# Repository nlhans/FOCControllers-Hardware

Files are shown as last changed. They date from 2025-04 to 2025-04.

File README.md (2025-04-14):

# FOCControllers
Exploring the world of FOC with BLDC/Steppers for custom haptic/force feedback in game controllers

Design is WIP.

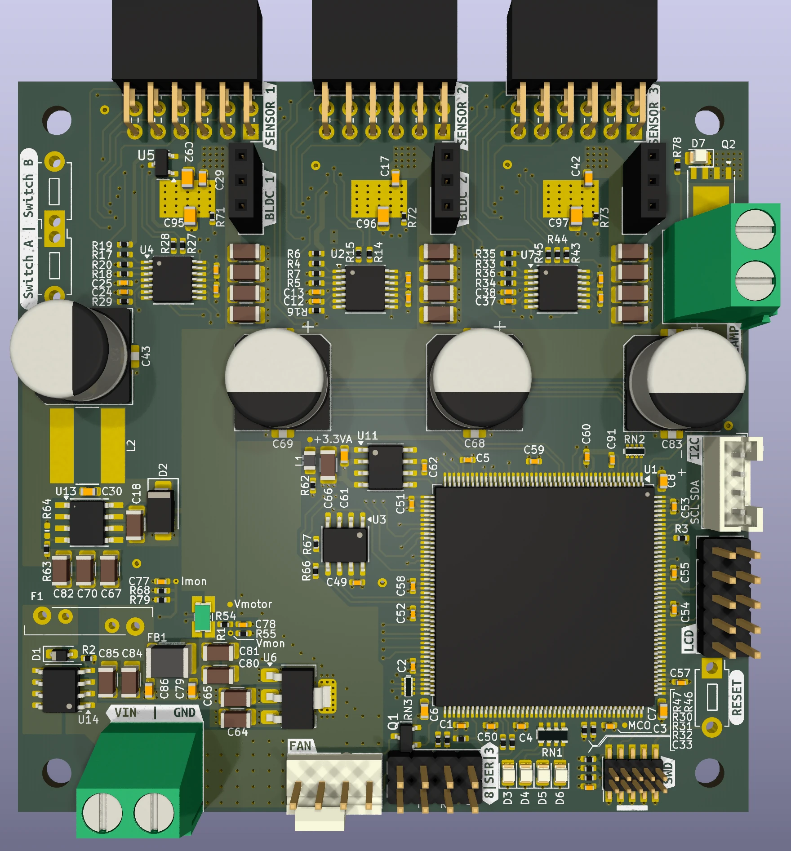
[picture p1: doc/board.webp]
PCB


## MCU
After some exploration, I've chosen to base this design around the STM32H725. There were several close runner ups, including some STM32G4 and F7 parts, and most honourable mention the RP2350. However, the RP2350 was not available from Mouser etc. at the time I started CAD. 
The secondary reason for the STM32H725 is that I still have a handful of these chips unassigned to a project in my parts bin. Considering they weren't cheap while coming in the "large brick" LQFP-176 package, this seemed like a good excuse to finally use them (-: 

Joking aside, this part is quite well suited for experiments with BLDC. Empirical observations using a Nucleo-H743 and the Arduino SimpleFOC library showed that the loopFOC() and move() functions take approximately 3.8 - 4.0us to execute on this chip (approx 1900 CPU cycles). This does not include sensor I/O. That means that running the FOC loop at 5-25kHz (depending on the position sensor datarate) will use around 2-10\% of CPU time. However, in this design I will be using this chip to drive 3 motors, which could bring up the CPU load to 30\%. 

This CPU time excludes I/O time from I2C/SPI bus transfers, or ADC data retrieval, "actual" FOC with DC current feedback, and more importantly, and force feedback algorithms. I would expect when this is all included that 25kHz loop speed would be quite the challenge.

I have also considered the RP2040, as I've used it for some exploration before concluding this design. However its lack of FPU and Cortex-M0+ could not do FOC loop calculations at more than 1kHz due to widespread floating point usage in SimpleFOC. Perhaps 2kHz was attainable when the slow I2C I/O is offloaded to the second core.. but 2kHz is still not a terrific loop speed. It didn't make sense to go through all that effort.

## Motor Driver
I have chosen to use the DRV8316C BLDC driver from Texas Instruments. This chip can use 6-PWM or 3-PWM mode with ENABLE input. The latter is necessary for SimpleFOC implementation of PWM and truth table to the (half-)H bridge drivers. Previous experiments with cheap DRV8833 boards were able to drive a BLDC motor, however, it was not controlling the DRV8833s properly due to its truth table orientated at brushed motor control (long story..). 

Moreover, the DRV8316C chip can operate with 24V supply. and drive 3-5A into motors. I plan to use this magnitude of power for developing an active pedal for simrig racing. These typically require motors in the order of 60-90Watt peak. 

The whole board will be fused for a continuous current of 5A. This may seem awkward to divide across 3 channels, but I expect the duty cycle and concurrent power output to be quite low for this application.

##  Sensing
The board contains, per motor channel, the interfaces for the following sensors:

- I2C magnetic encoders (e.g. As5600)
- SPI or Infineon SSC magnetic encoders (e.g. TLE5012B or TLI5012B)
- Lineair Potentiometer
- NTC for motor temperature
- Current Sense for all 3 coil outputs

The analog sensor channels are connected to a dedicated ADC on the STM32H7 each. The chip will be programmed to convert all channels on each FOC cycle.

All analog channels are referenced against a 3.0V voltage reference. BLDC channel 1 contains a 3.0V regulator to power the analog electronics for all 3 motor channels.

## Other stuff
The PCB contains several support functions which should aid for a configurable & robust driver:

- I2C 24AAxx EEPROM (bitbanged)
- I2C temperature sensor near driver of channel 2 (bitbanged)
- Voltage/Current monitor of input supply
- 5V/Vin 4-pin PWM fan with tacho readout. The board has a 80x80mm form factor in case it runs hot.
- Power clamp to dump regen power (if necessary).
- SPI interface for driving a small LCD
- I2C Grove Connector (hardware I2C)
- 2 UARTs
- 4 Debug LEDs
- 2 Push Buttons
- SWD debug

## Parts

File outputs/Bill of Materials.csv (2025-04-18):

Id | Designator | Footprint | Quantity | Designation | Supplier and ref
1 | R82,R81,R67,R78,R55,R66,R56,R59,R60,R76,R61,R58,R77,R57 | Nice_0402R | 14 | 1k
2 | D9,D8,D6,D5,D7,D3,D4 | LED_0805_2012Metric | 7 | APT2012SYCK
3 | C97,C96,C95,C92,C8,C6,C7 | Nice_0603C | 7 | 2.2u
4 | R68,R79 | Nice_0402R | 2 | 15k
5 | R19,R5,R34,R32,R35,R8,R36,R4,R6,R7,R20,R54,R33,R31,R3,R17,R18,R30,R9 | Nice_0402R | 19 | 10k
6 | TP54,TP56,TP53,TP59,TP55,TP22,TP75,TP47,TP36,TP49,TP70,TP69,TP41,TP74,TP35,TP23,TP12,TP20,TP24,TP66,TP31,TP40,TP32,TP48,TP76,TP39,TP17,TP43,TP65,TP16,TP34,TP64,TP63,TP71,TP25,TP61,TP58,TP51,TP15,TP73,TP52,TP33,TP10,TP68,TP42,TP14,TP28,TP29,TP77,TP38,TP26,TP45,TP44,TP11,TP72,TP13,TP46,TP62,TP30,TP21,TP57,TP37,TP67,TP19,TP60,TP27,TP50,TP18 | TP_0.6mm | 68 | TestPoint
7 | C50,C91,C25,C51,C3,C49,C57,C77,C78,C33,C2,C55,C54,C60,C5,C4,C13,C53,C58,C59,C52,C1,C38,C56,C40,C9,C89,C34,C15,C88,C27,C21,C63,C26 | Nice_0402C | 34 | 100n
8 | R44,R29,R15,R27,R45,R43,R14,R28,R16 | Nice_0402R | 9 | 820R
9 | J12,J5 | TerminalBlock_Phoenix_MKDS-1,5-2_1x02_P5.00mm_Horizontal | 2 | Screw_Terminal_01x02
10 | C72,C31,C20,C74,C85,C19,C18,C84,C66,C80,C70,C75,C65,C71,C82,C76,C67,C81,C44,C73,C45,C64,C32 | C_1206_3216Metric | 23 | 10u
11 | R2 | Nice_0402R | 1 | 100k
12 | SW3,SW2,SW1 | SW_PUSH_1P1T_6x3.5mm_H5.0_APEM_MJTP1250 | 3 | SW_Push
13 | R71,R47,R46,R73,R63,R72,R49 | Nice_0402R | 7 | 0R
14 | U2,U4,U7 | TSSOP-14_4.4x5mm_P0.65mm | 3 | LM324
15 | J11,J9 | PinHeader_1x04_P2.54mm_Vertical | 2 | Conn_01x04
16 | R69,R75,R62,R74,R70 | Nice_0402R | 5 | 100R
17 | J4 | PinHeader_2x05_P2.54mm_Vertical | 1 | Conn_02x05_Odd_Even
18 | R1 | R_Shunt_Ohmite_LVK12 | 1 | LVK12R020
19 | U3 | SOIC-8_3.9x4.9mm_P1.27mm | 1 | 24LC64
20 | SWD1 | PinHeader_2x05_P1.27mm_Vertical_SMD | 1 | Conn_02x05_Odd_Even
21 | C11,C12,C35,C23,C36,C37,C22,C10,C24 | Nice_0402C | 9 | 100p
22 | R80 | Nice_0402DNP | 1 | DNP
23 | U6 | SOT-223-3_TabPin2 | 1 | AMS1117-3.3
24 | C86,C79,C90,C42,C17,C29 | Nice_0603C | 6 | 100n
25 | J8,J7,J6 | PinSocket_1x03_P2.54mm_Vertical | 3 | Conn_01x03_Pin
26 | M1 | FanPinHeader_1x04_P2.54mm_Vertical | 1 | Fan_Tacho_PWM
27 | FB1 | L_1812_4532Metric | 1 | 74279223560
28 | J1,J3,J2 | PinSocket_2x06_P2.54mm_Horizontal | 3 | Conn_02x06_Odd_Even
29 | RN1 | R_Array_Convex_4x0603 | 1 | EXB-38V102JV
30 | RN2,RN3,RN4,RN5 | R_Array_Concave_4x0402 | 4 | EXB-N8N220JX
31 | Q1 | SOT-23 | 1 | 2N7002
32 | L2 | L_Bourns-SRN8040_8x8.15mm | 1 | 22u
33 | C69,C68,C83 | CP_Elec_10x10.5 | 3 | 330uF
34 | C61,C28,C16,C41 | Nice_0603C | 4 | 1u
35 | C30 | Nice_0603C | 1 | 10n
36 | U11 | SOIC-8_3.9x4.9mm_P1.27mm | 1 | MCP1501-25E/SN
37 | U1 | LQFP-176_24x24mm_P0.5mm | 1 | STM32H725IGTx
38 | F1 | LIttelfuse_30R | 1 | 30R500U
39 | R64,R48 | Nice_0402DNP | 2 | TBD
40 | D2 | D_SMA | 1 | SS16
41 | L1 | L_0805_2012Metric | 1 | BLM18AG471SN1D
42 | C43 | CP_Elec_8x10.5 | 1 | 330uF
43 | U14 | SOIC-8_3.9x4.9mm_P1.27mm | 1 | Si4435DDY
44 | U13 | TI_SO-PowerPAD-8 | 1 | LM22676MR-5
45 | J10 | JST_PH_B4B-PH-K_1x04_P2.00mm_Vertical | 1 | Conn_01x04
46 | D1 | D_SOD-323_HandSoldering | 1 | BZX384-B10,115
47 | Q2 | PowerPAK_SO-8_Single | 1 | SIR422DP-T1-GE3
48 | U5 | SOT-23 | 1 | AP7375-30SA-7
49 | C62 | Nice_0402C | 1 | 1n
50 | Y1 | Crystal_SMD_3225-4Pin_3.2x2.5mm | 1 | ECS-250-18-33-JGN-TR3
51 | U16,U10,U15 | VQFN40_RGF_TEX | 3 | DRV8316CR
52 | U12 | WSON-8-1EP_2x2mm_P0.5mm_EP0.9x1.6mm_ThermalVias | 1 | TMP1075DSG
53 | C39,C48,C87 | Nice_0603C | 3 | 47n
54 | U17 | SOT-23 | 1 | ZXCT1109
55 | R65,R51,R50,R52 | Nice_0402R | 4 | 470R
56 | TP6,TP1,TP4,TP7,TP2,TP5,TP8,TP3 | TestPoint_THTPad_D1.0mm_Drill0.5mm | 8 | TestPoint
57 | C46,C47 | Nice_0402C | 2 | 18p

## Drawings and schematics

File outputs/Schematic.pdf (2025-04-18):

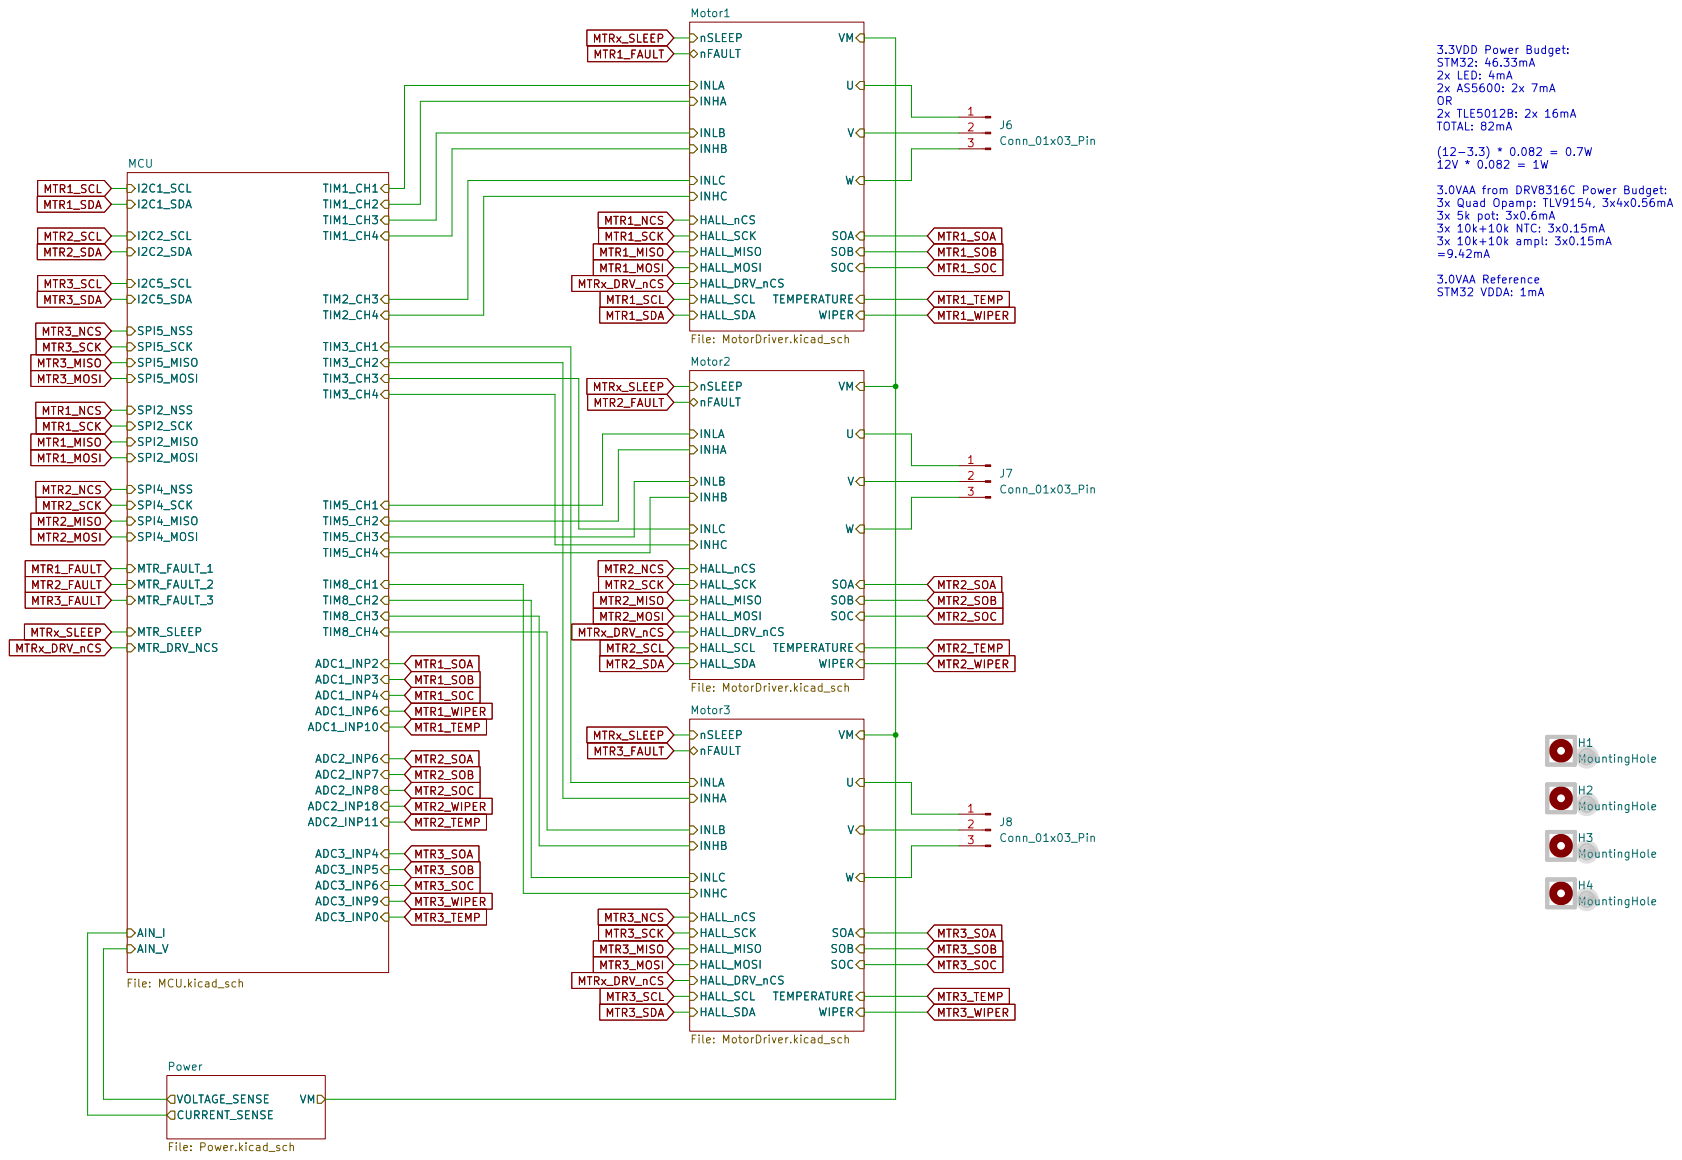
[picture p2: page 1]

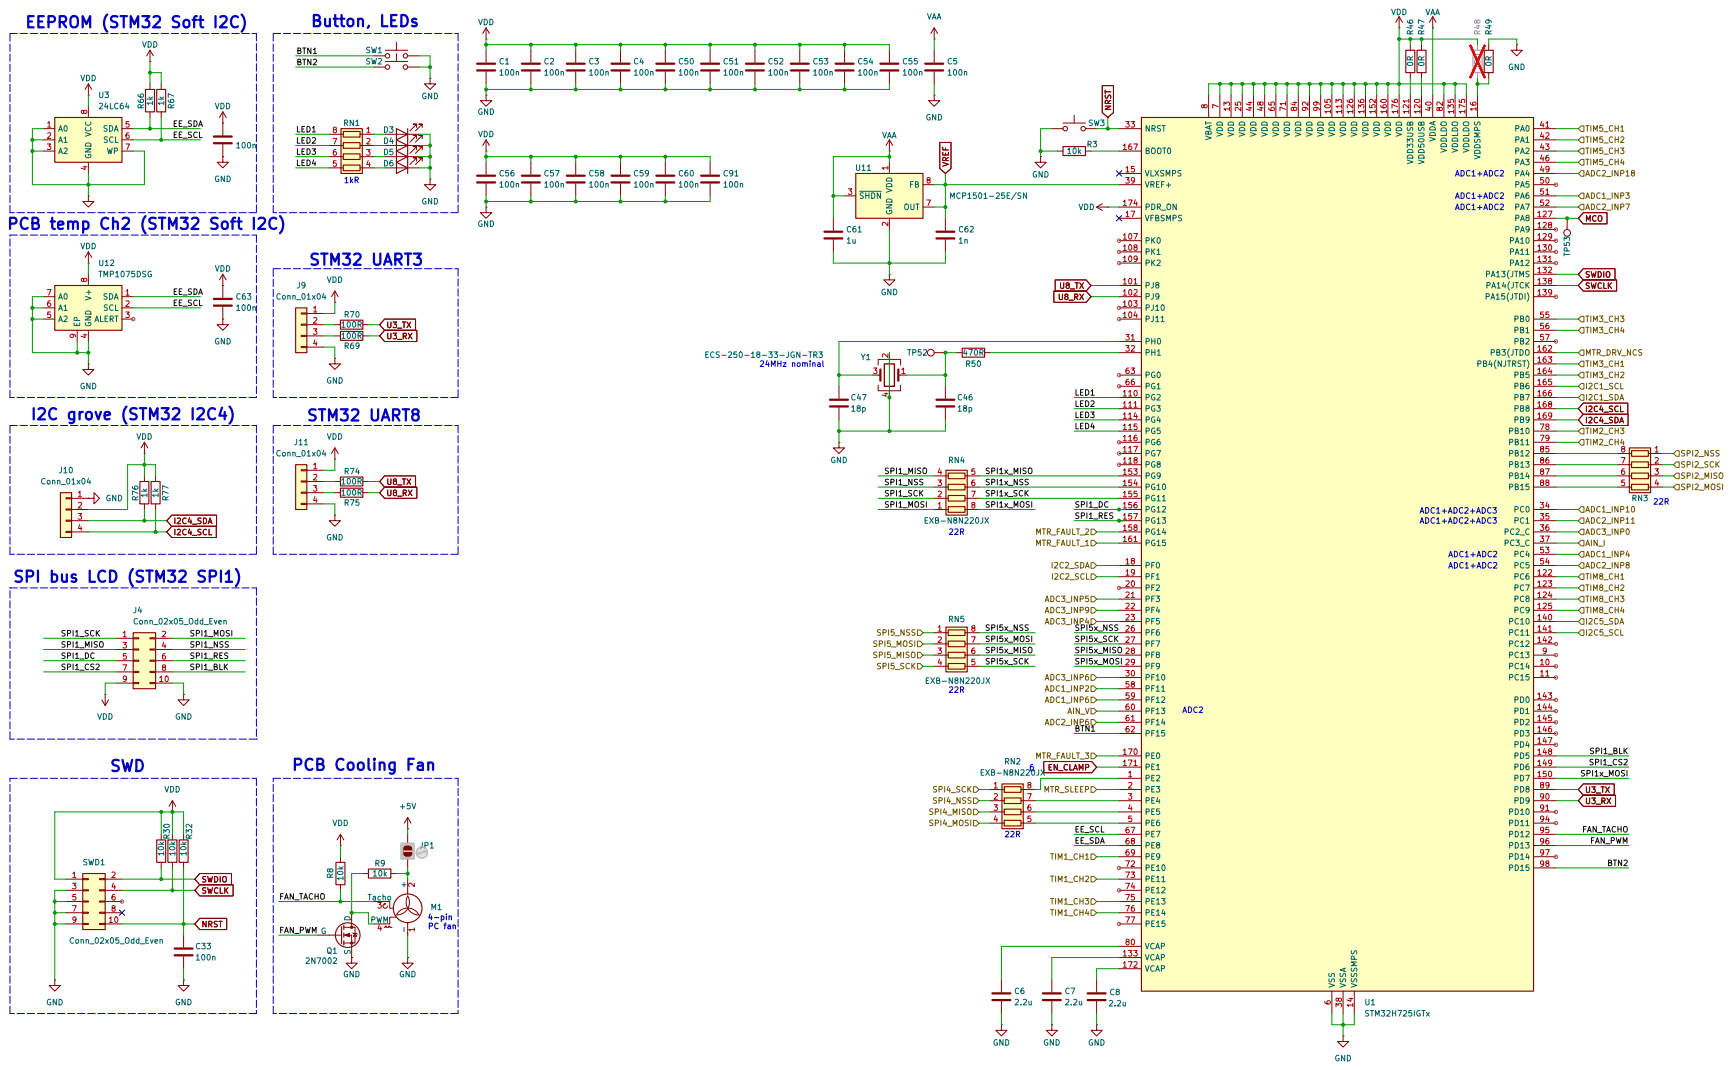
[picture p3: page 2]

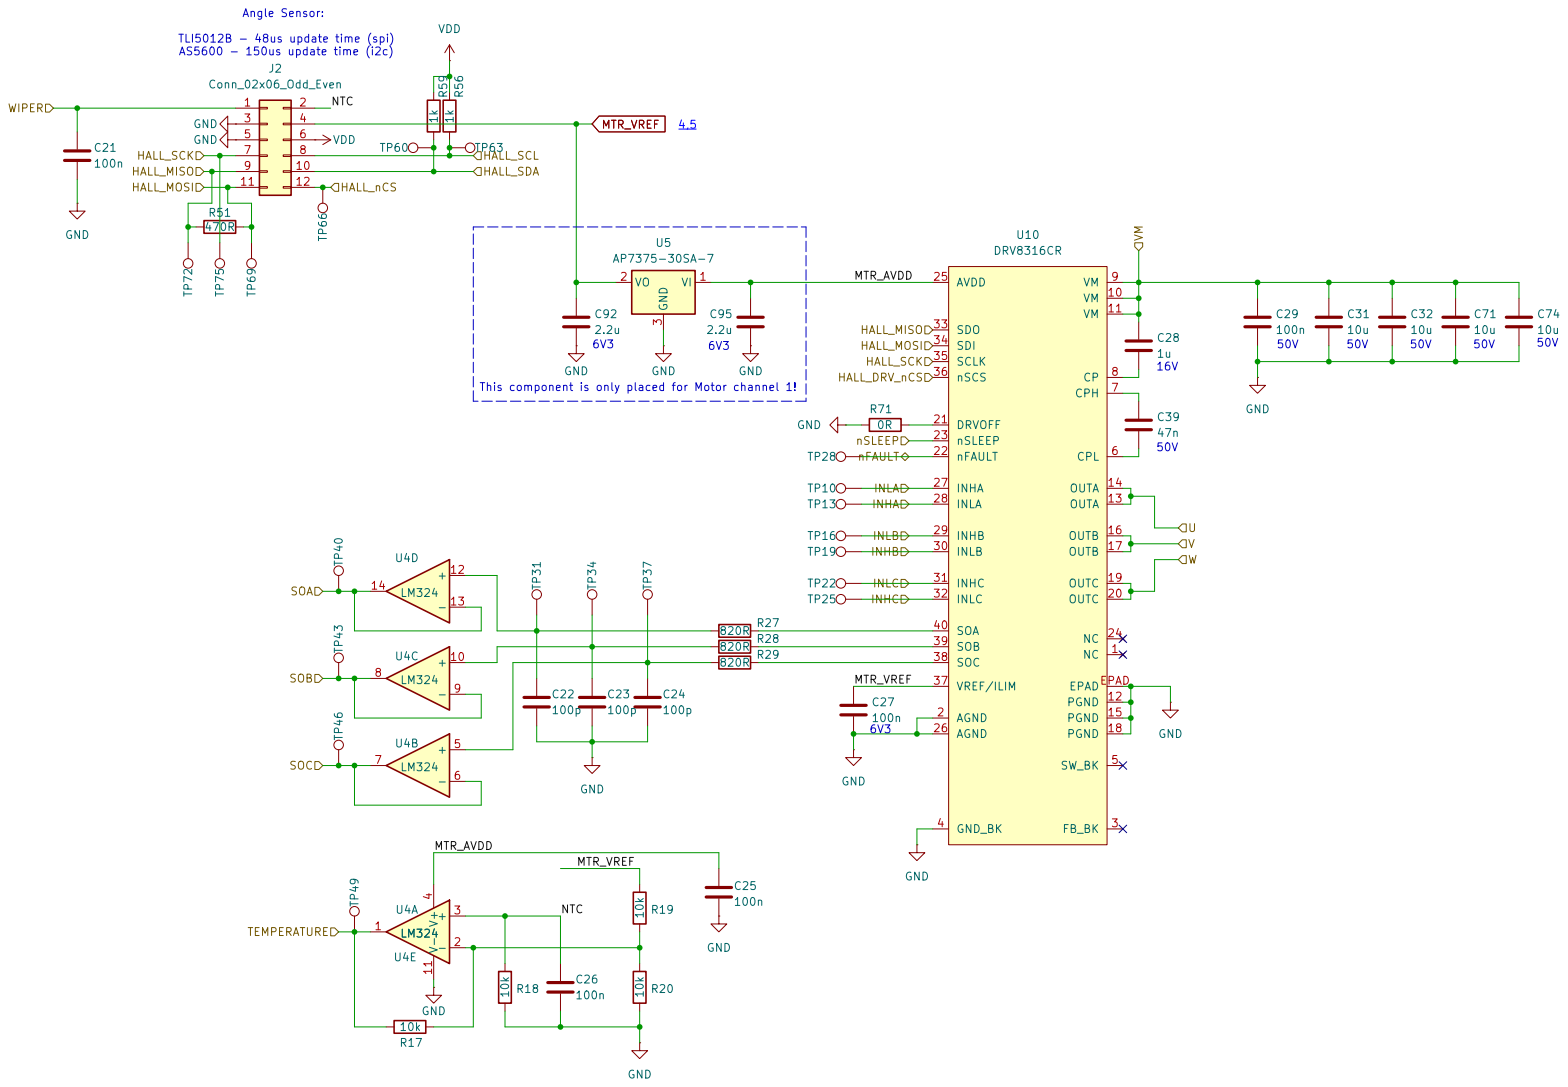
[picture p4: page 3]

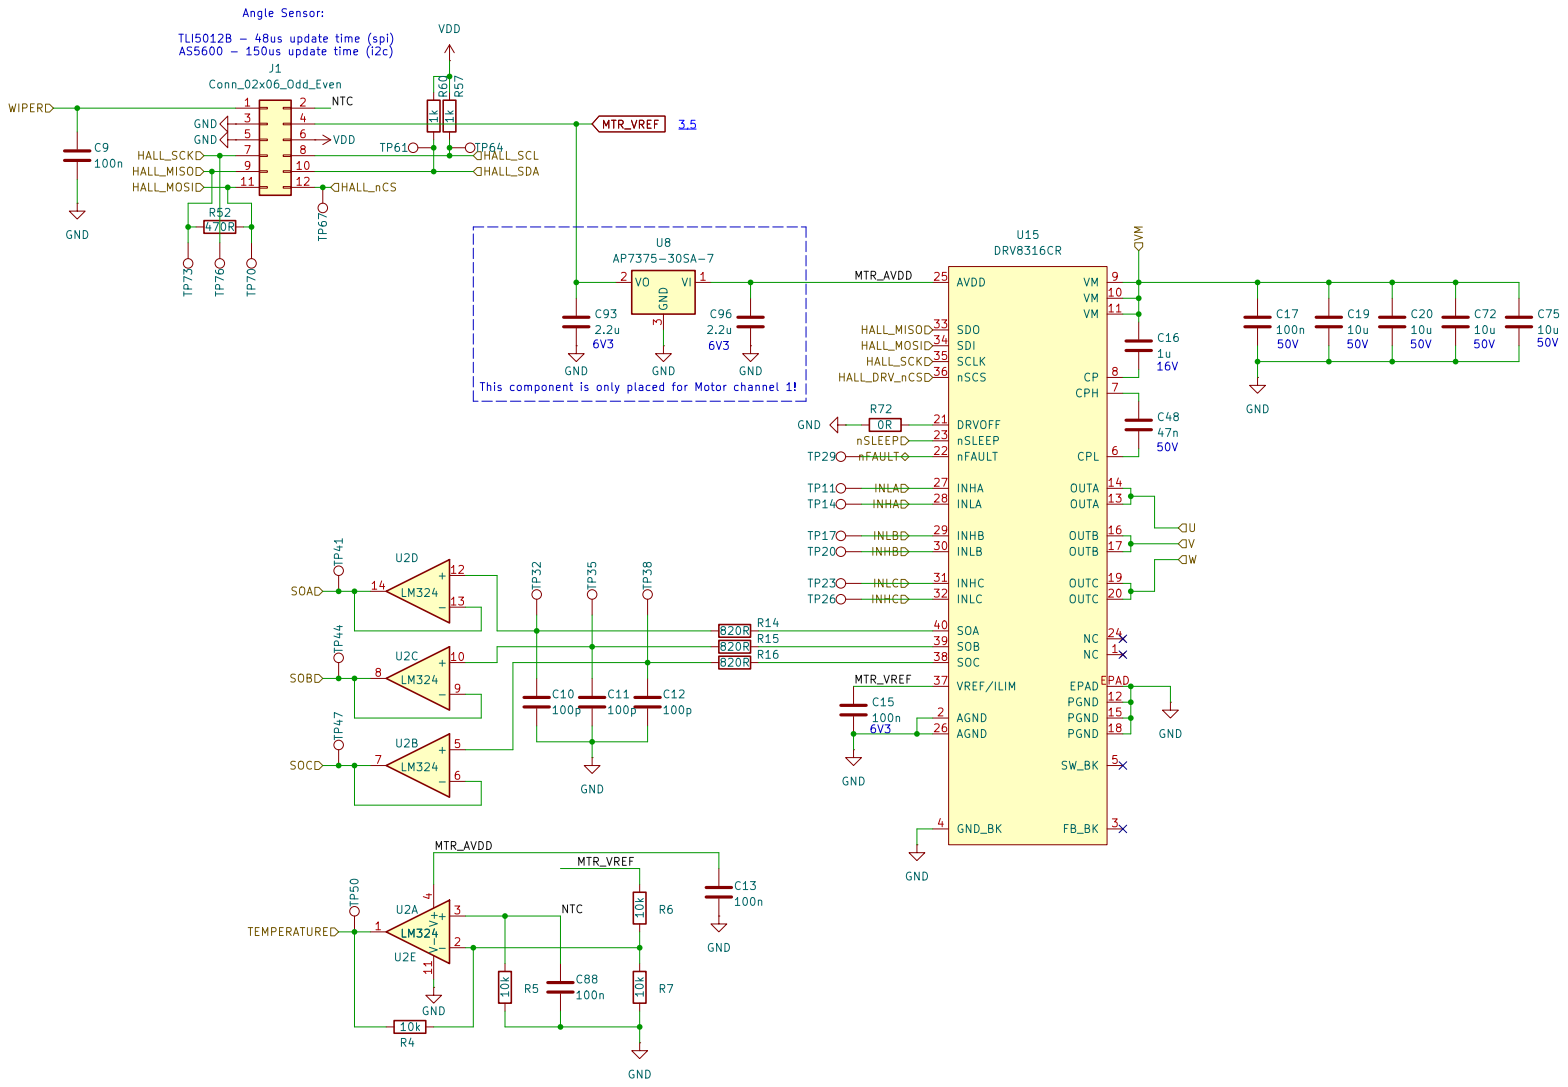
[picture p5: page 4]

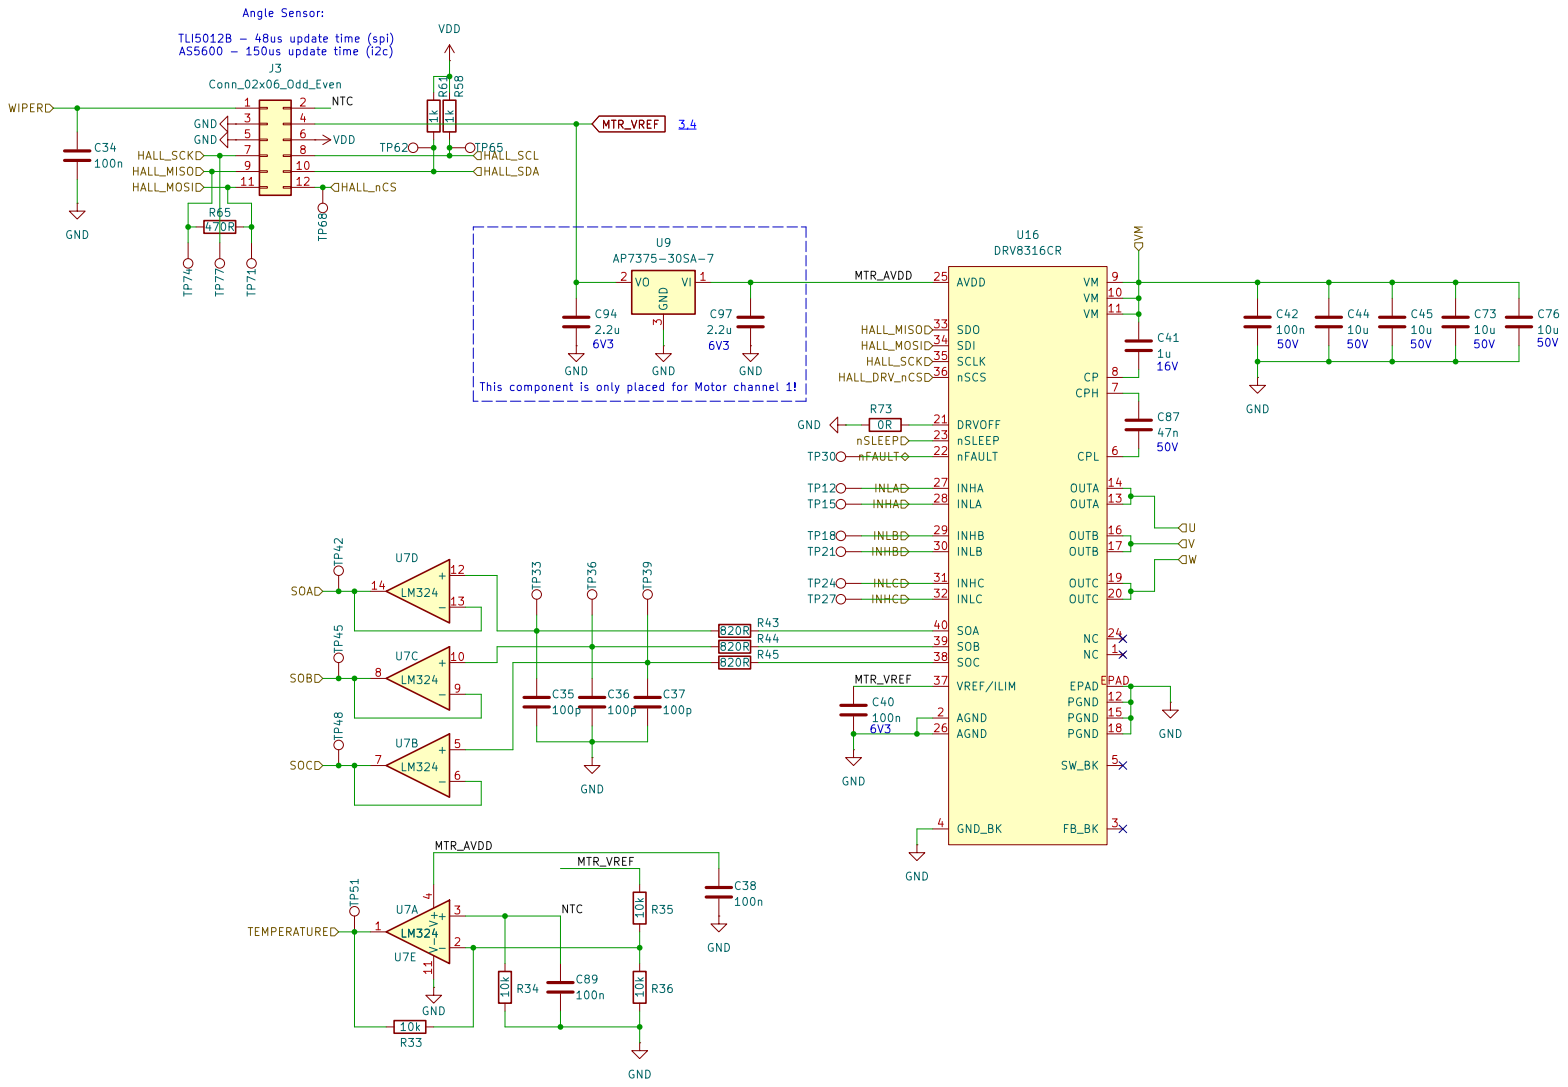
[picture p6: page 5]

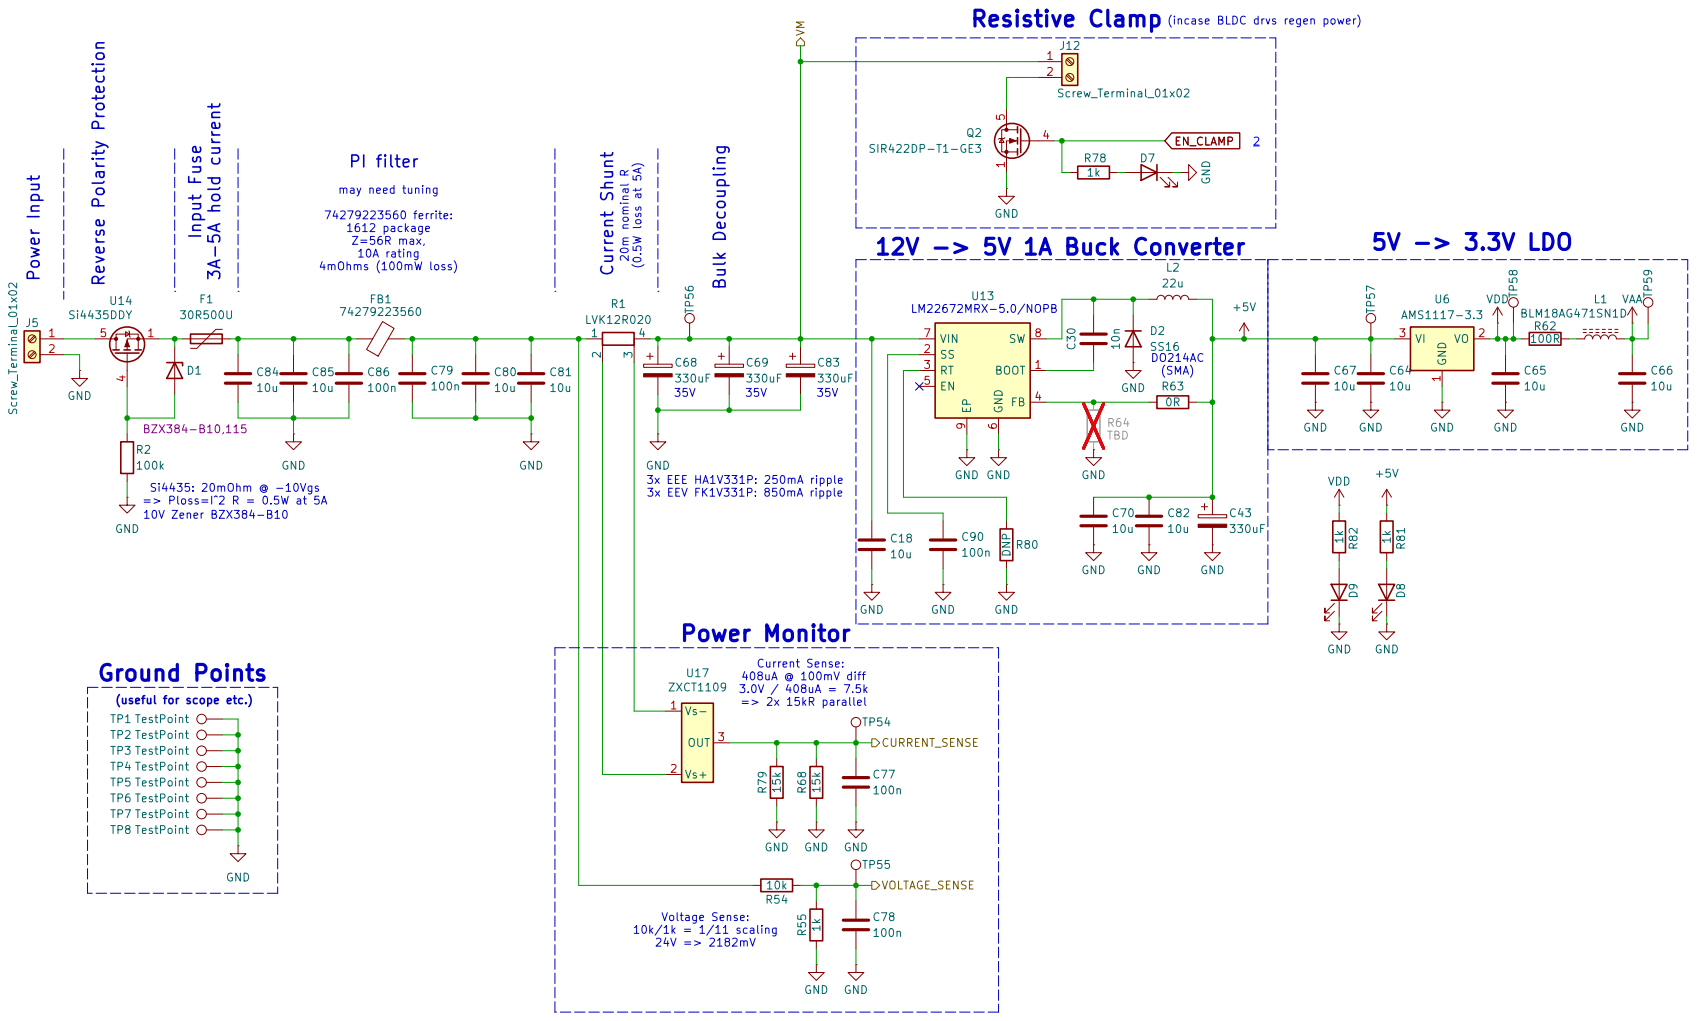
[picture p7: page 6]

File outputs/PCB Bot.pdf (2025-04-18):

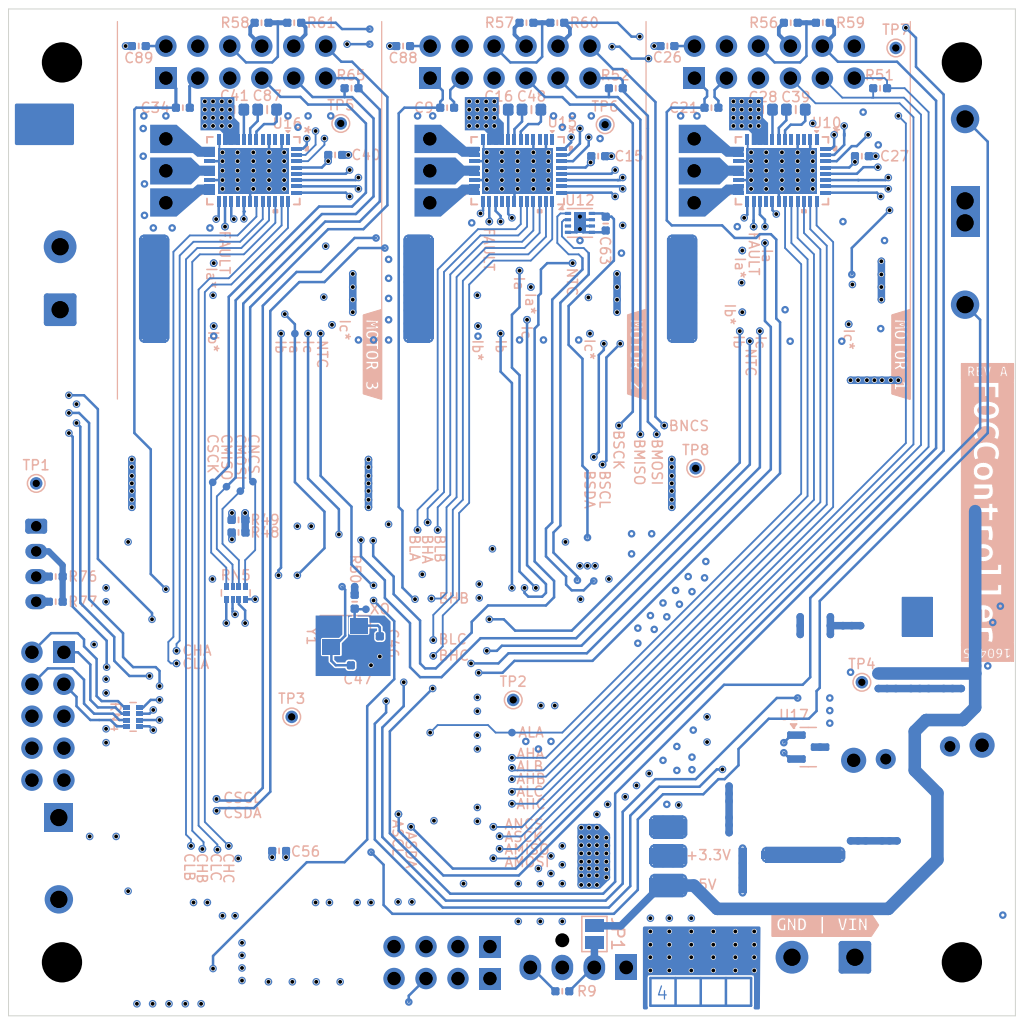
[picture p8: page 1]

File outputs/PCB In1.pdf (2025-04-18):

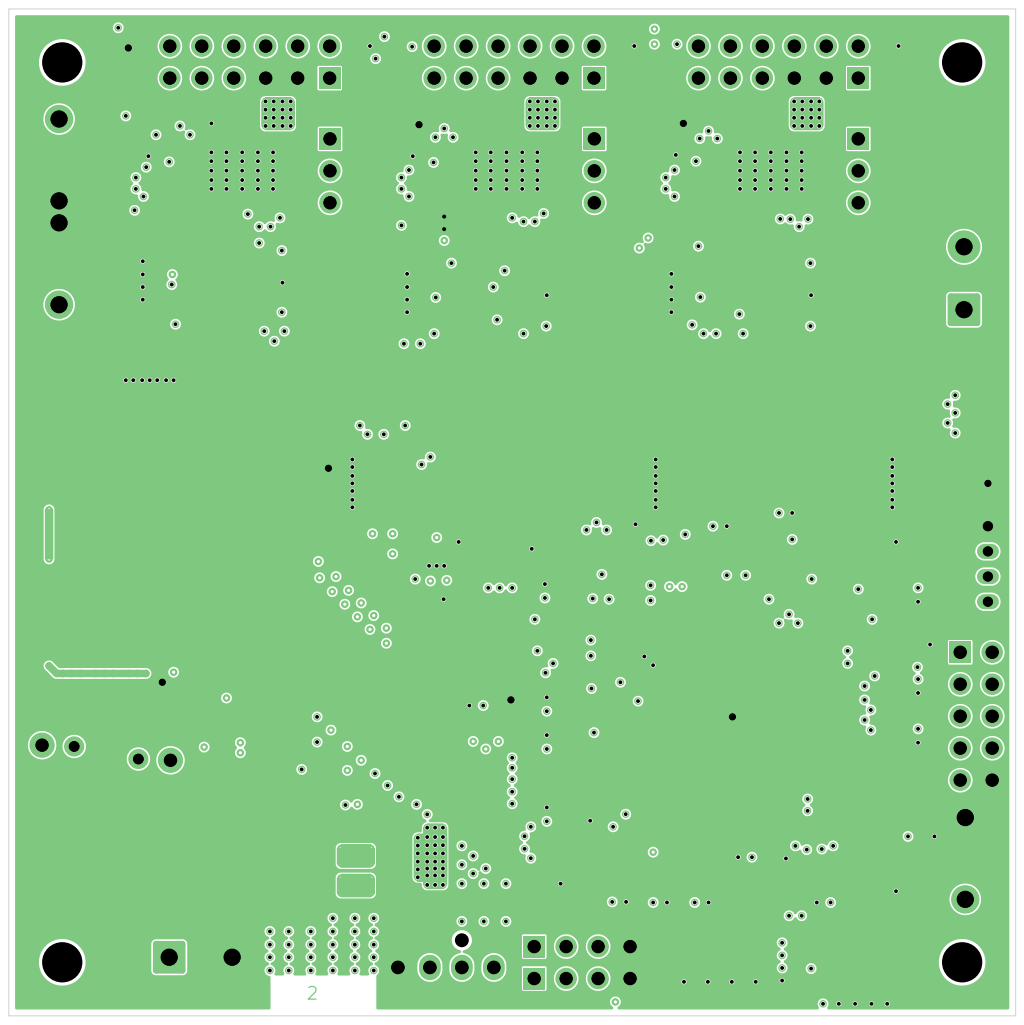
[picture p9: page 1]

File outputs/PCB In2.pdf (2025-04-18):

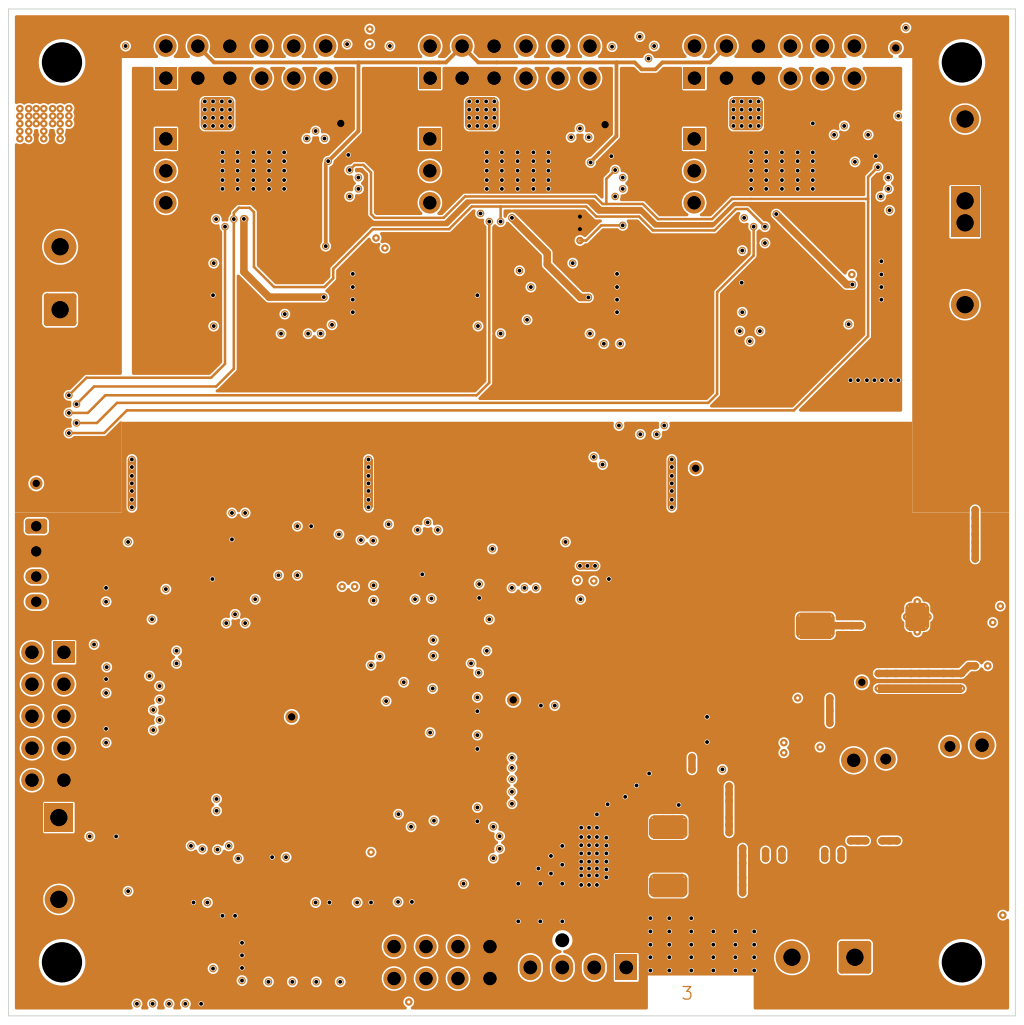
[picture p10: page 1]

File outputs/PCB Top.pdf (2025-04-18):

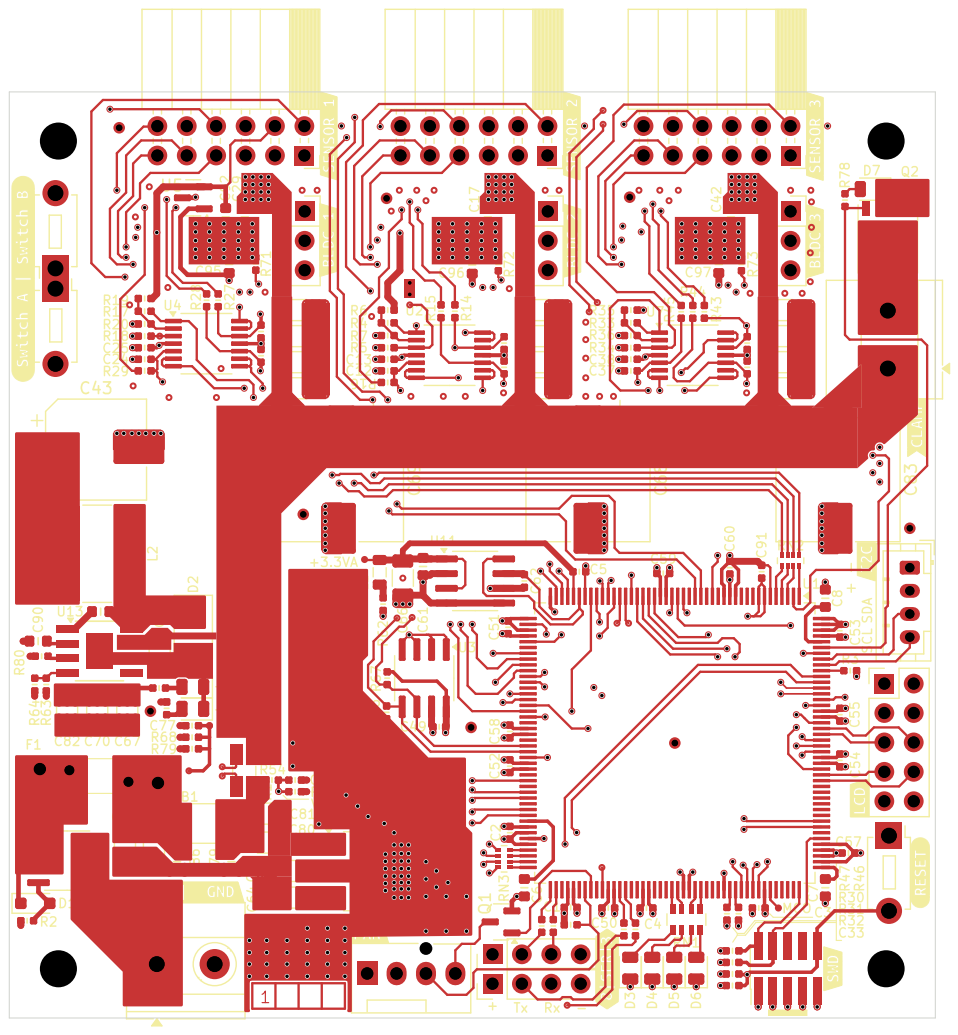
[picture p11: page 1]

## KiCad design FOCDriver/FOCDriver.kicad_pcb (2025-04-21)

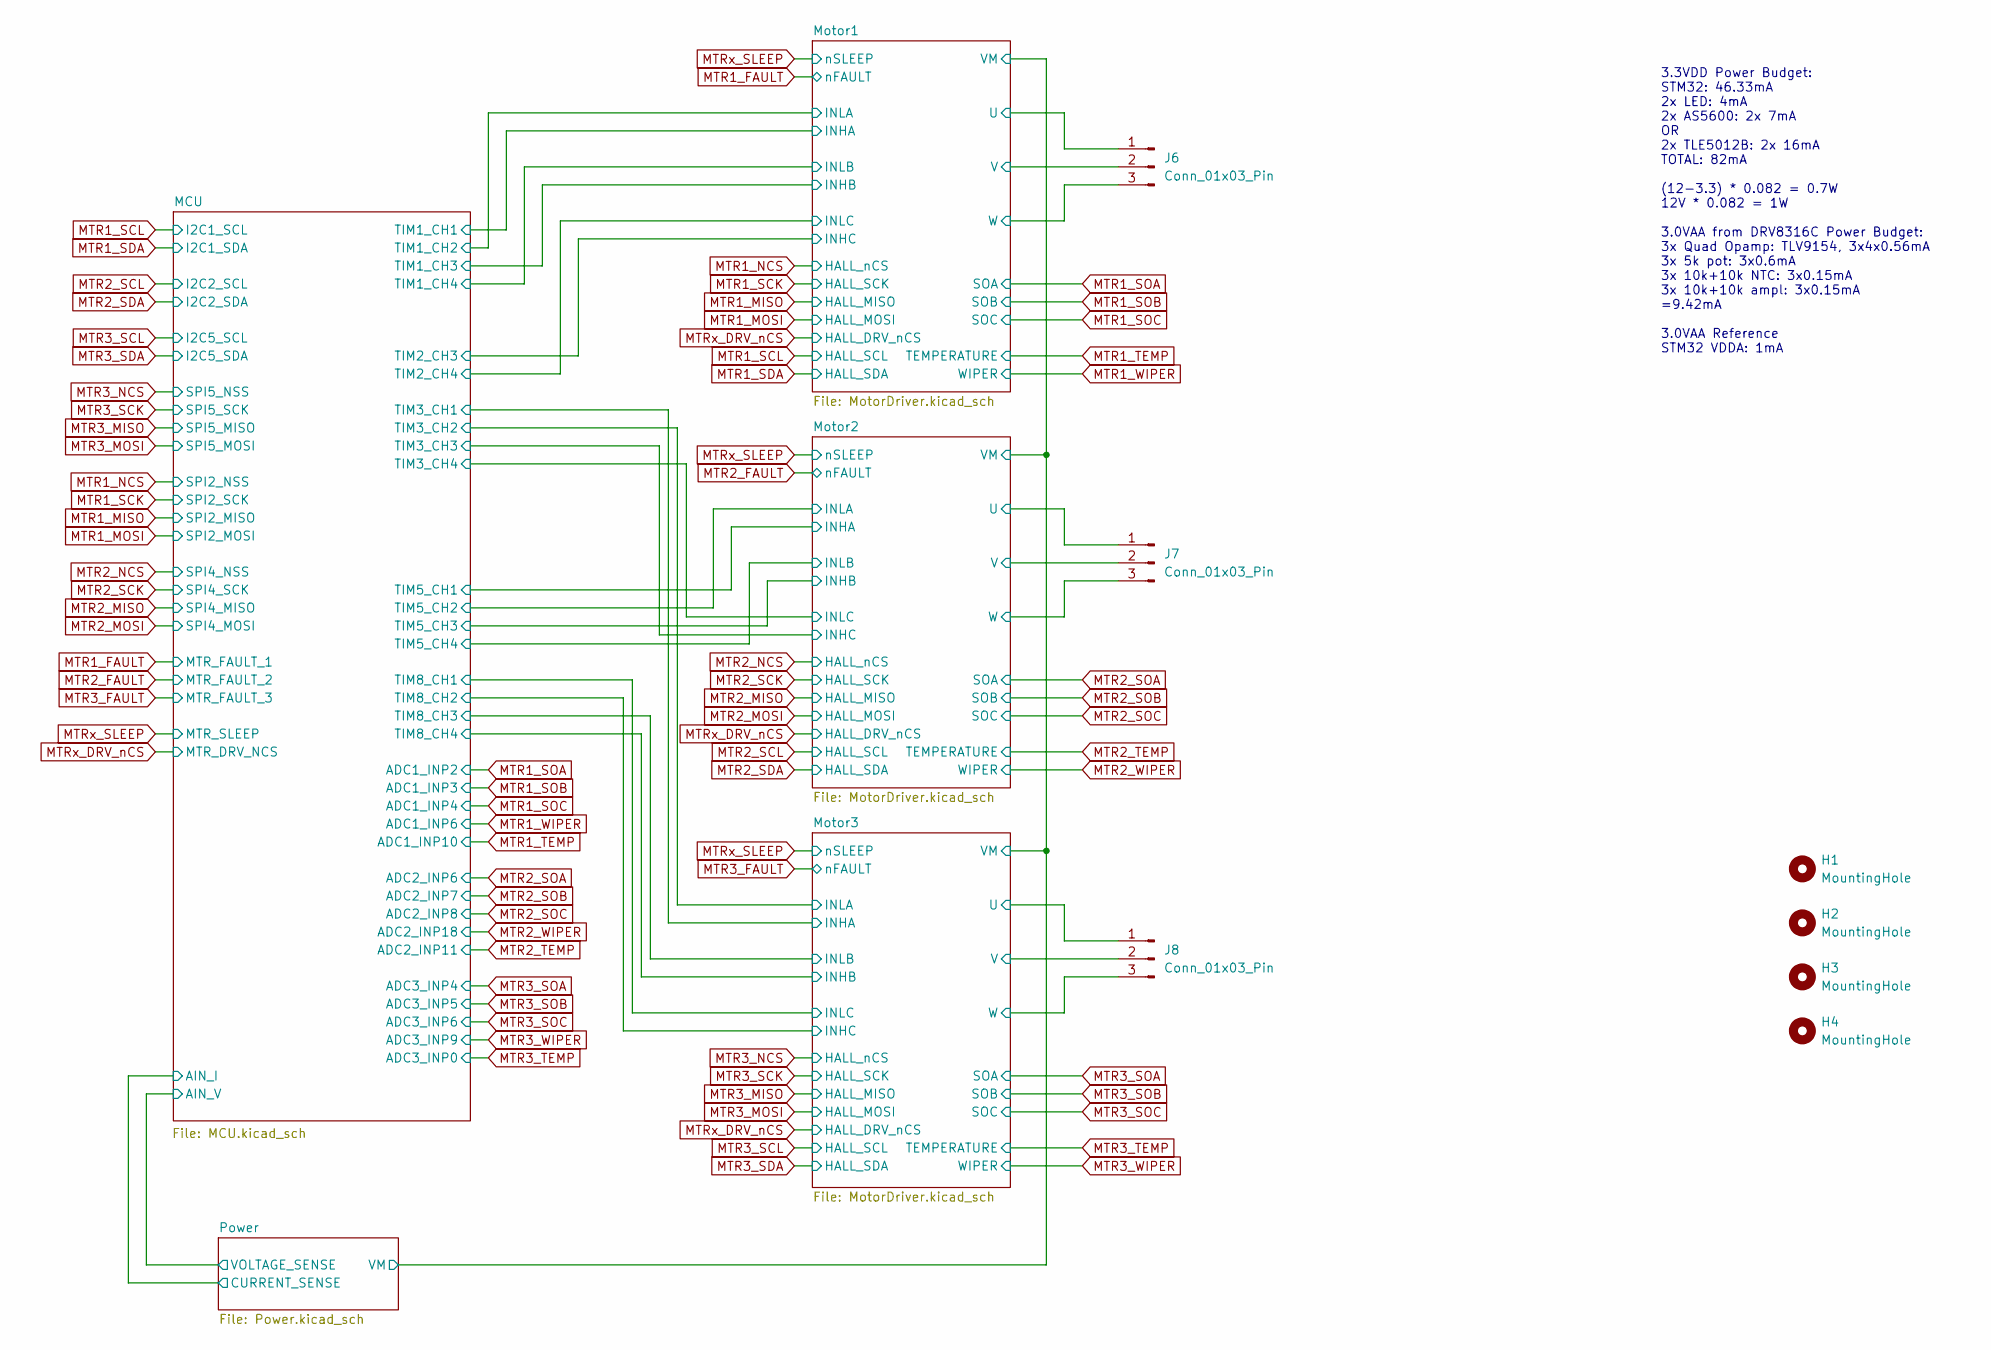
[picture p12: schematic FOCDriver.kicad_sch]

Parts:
H1, H2, H3, H4: MountingHole; MountingHole_3.2mm_M3
J6, J7, J8: Conn_01x03_Pin; PinSocket_1x03_P2.54mm_Vertical

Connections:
/Motor1/U: J6.1; also elsewhere on the board
/Motor1/V: J6.2; also elsewhere on the board
/Motor1/W: J6.3; also elsewhere on the board
/Motor2/U: J7.1; also elsewhere on the board
/Motor2/V: J7.2; also elsewhere on the board
/Motor2/W: J7.3; also elsewhere on the board
/Motor3/U: J8.1; also elsewhere on the board
/Motor3/V: J8.2; also elsewhere on the board
/Motor3/W: J8.3; also elsewhere on the board

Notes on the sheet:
3.3VDD Power Budget: STM32: 46.33mA 2x LED: 4mA 2x AS5600: 2x 7mA OR 2x TLE5012B: 2x 16mA TOTAL: 82mA (12-3.3) * 0.082 = 0.7W 12V * 0.082 = 1W 3.0VAA from DRV8316C Power Budget: 3x Quad Opamp: TLV9154, 3x4x0.56mA 3x 5k pot: 3x0.6mA 3x 10k+10k NTC: 3x0.15mA 3x 10k+10k ampl: 3x0.15mA =9.42mA 3.0VAA R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

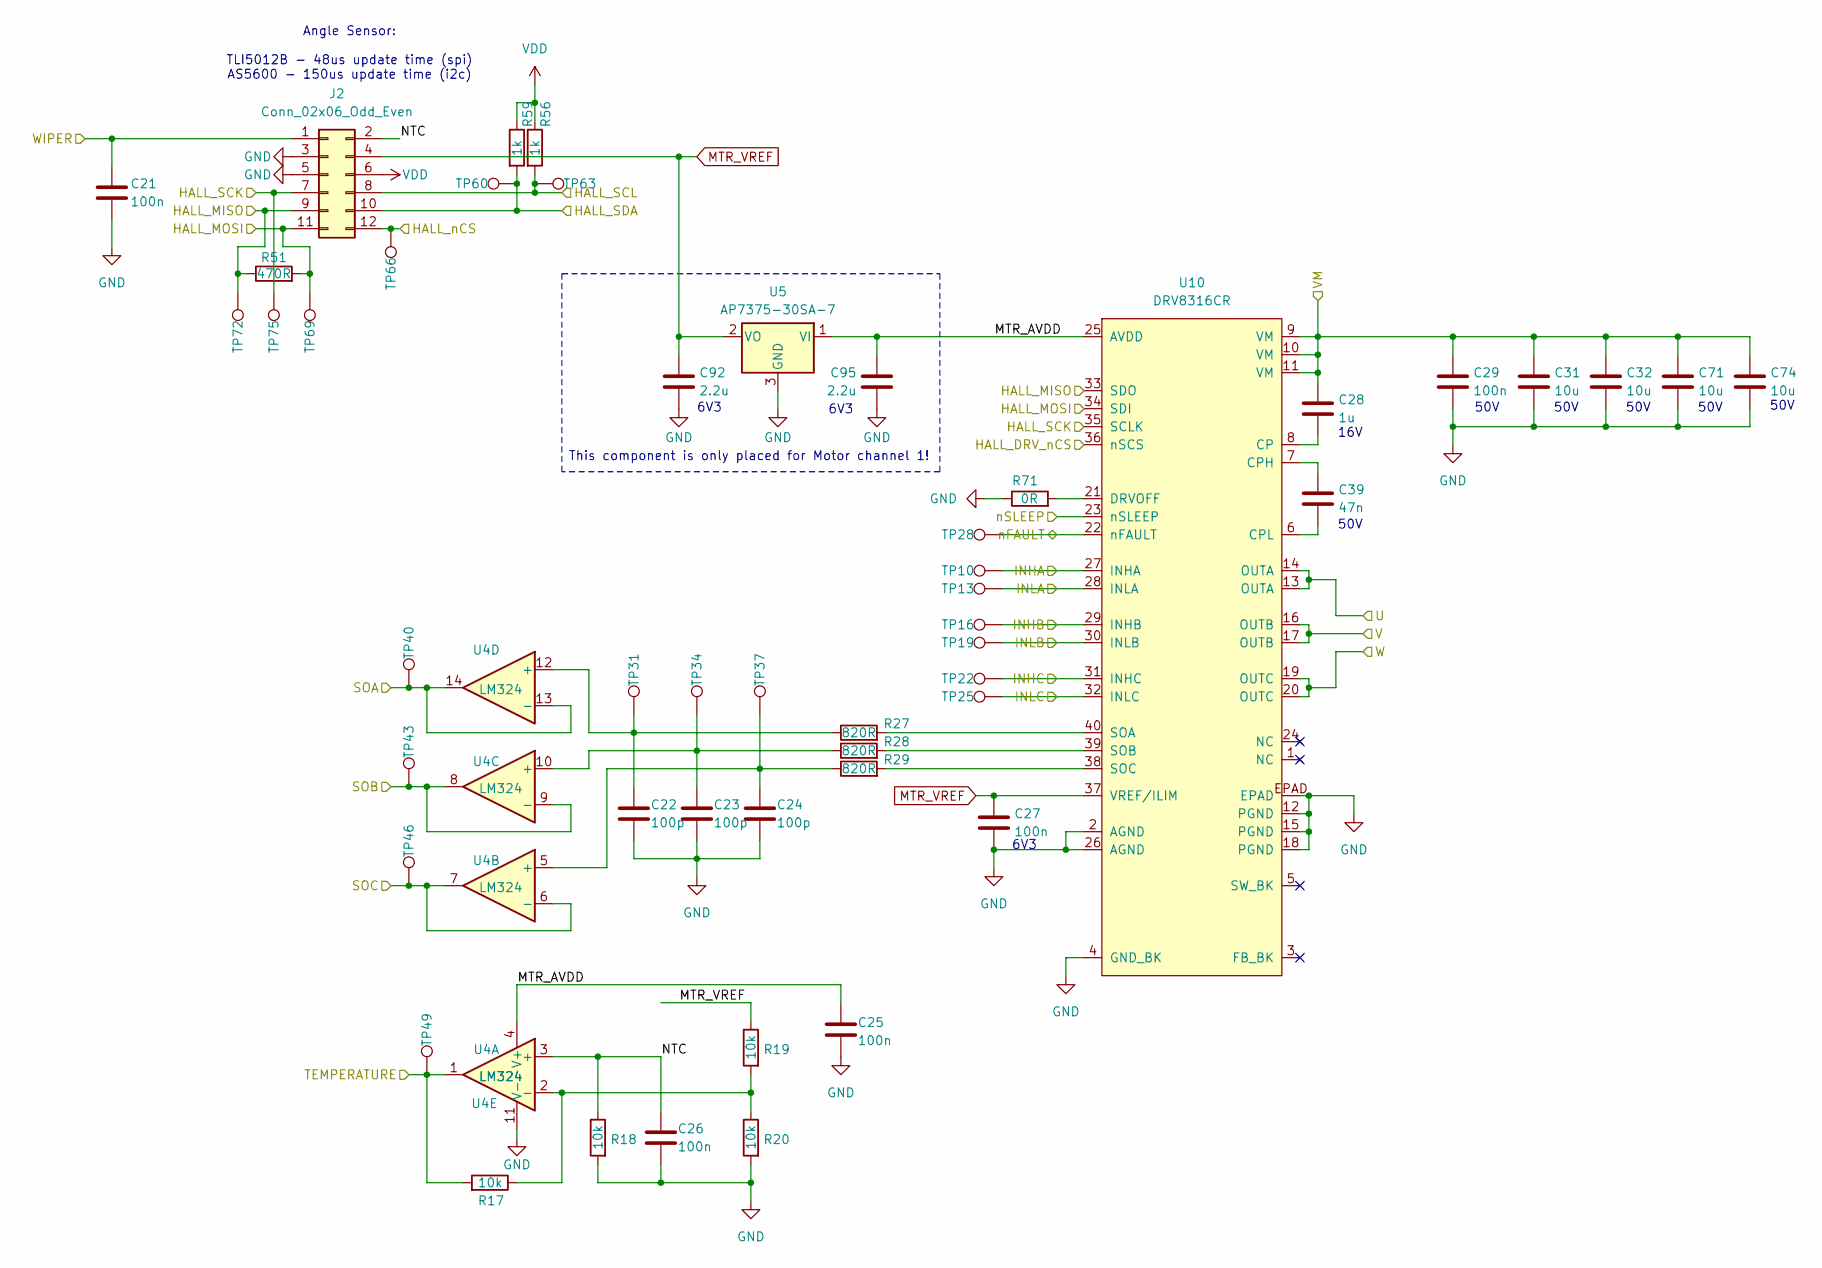
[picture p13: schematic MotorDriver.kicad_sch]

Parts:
C21, C25, C26, C27: 100n; Nice_0402C
C22, C23, C24: 100p; Nice_0402C
C28: 1u; Nice_0603C
C29: 100n; Nice_0603C
C31, C32, C71, C74: 10u; C_1206_3216Metric
C39: 47n; Nice_0603C
C92, C95: 2.2u; Nice_0603C
J2: Conn_02x06_Odd_Even; PinSocket_2x06_P2.54mm_Horizontal
R17, R18, R19, R20: 10k; Nice_0402R
R27, R28, R29: 820R; Nice_0402R
R51: 470R; Nice_0402R
R56, R59: 1k; Nice_0402R
R71: 0R; Nice_0402R
TP10, TP13, TP16, TP19, TP22, TP25, TP28, TP31, TP34, TP37, TP40, TP43, TP46, TP49, TP60, TP63, TP66, TP69, TP72, TP75: TestPoint; TP_0.6mm
U4: LM324; TSSOP-14_4.4x5mm_P0.65mm
U5: AP7375-30SA-7; SOT-23; MPN AP7375-30SA-7
U10: DRV8316CR; VQFN40_RGF_TEX; MPN DRV8316CRRGFR

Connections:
/MCU/TIM1_CH1: TP10.1, U10.27 (INHA); also elsewhere on the board
/MCU/TIM1_CH2: TP13.1, U10.28 (INLA); also elsewhere on the board
/MCU/TIM1_CH3: TP16.1, U10.29 (INHB); also elsewhere on the board
/MCU/TIM1_CH4: TP19.1, U10.30 (INLB); also elsewhere on the board
/MCU/TIM2_CH3: TP22.1, U10.31 (INHC); also elsewhere on the board
/MCU/TIM2_CH4: TP25.1, U10.32 (INLC); also elsewhere on the board
/Motor1/MTR_AVDD: C25.1, C95.1, U4.4 (V+), U5.1 (VI), U10.25 (AVDD)
/Motor1/NTC: C26.1, J2.2, R18.1, U4.3 (+)
/Motor1/U: U10.13 (OUTA), U10.14 (OUTA); also elsewhere on the board
/Motor1/V: U10.16 (OUTB), U10.17 (OUTB); also elsewhere on the board
/Motor1/VM: C28.1, C29.1, C31.1, C32.1, C71.1, C74.1, U10.9 (VM), U10.10 (VM), U10.11 (VM); also elsewhere on the board
/Motor1/W: U10.19 (OUTC), U10.20 (OUTC); also elsewhere on the board
GND: C21.2, C22.2, C23.2, C24.2, C25.2, C26.2, C27.2, C29.2, C31.2, C32.2, C71.2, C74.2, C92.2, C95.2, J2.3, J2.5, R18.2, R20.2, R71.1, U4.11 (V-), U5.3 (GND), U10.2 (AGND), U10.4 (GND_BK), U10.12 (PGND), U10.15 (PGND), U10.18 (PGND), U10.26 (AGND), U10.EPAD; also elsewhere on the board
MTR1_FAULT: TP28.1, U10.22 (nFAULT); also elsewhere on the board
MTR1_MISO: J2.9, R51.1, TP72.1, U10.33 (SDO); also elsewhere on the board
MTR1_MOSI: J2.11, R51.2, TP69.1, U10.34 (SDI); also elsewhere on the board
MTR1_NCS: J2.12, TP66.1; also elsewhere on the board
MTR1_SCK: J2.7, TP75.1, U10.35 (SCLK); also elsewhere on the board
MTR1_SCL: J2.8, R56.2, TP63.1; also elsewhere on the board
MTR1_SDA: J2.10, R59.2, TP60.1; also elsewhere on the board
MTR1_SOA: TP40.1, U4.13 (-), U4.14; also elsewhere on the board
MTR1_SOB: TP43.1, U4.8, U4.9 (-); also elsewhere on the board
MTR1_SOC: TP46.1, U4.6 (-), U4.7; also elsewhere on the board
MTR1_TEMP: R17.2, TP49.1, U4.1; also elsewhere on the board
MTR1_WIPER: C21.1, J2.1; also elsewhere on the board
MTR_VREF: C27.1, C92.1, J2.4, R19.1, U5.2 (VO), U10.37 (VREF/ILIM); also elsewhere on the board
MTRx_DRV_nCS: U10.36 (nSCS); also elsewhere on the board
MTRx_SLEEP: U10.23 (nSLEEP); also elsewhere on the board
unnamed: R17.1, R19.2, R20.1, U4.2 (-)
unnamed: C24.1, R29.1, TP37.1, U4.5 (+)
unnamed: C23.1, R28.1, TP34.1, U4.10 (+)
unnamed: C22.1, R27.1, TP31.1, U4.12 (+)
unnamed: C28.2, U10.8 (CP)
unnamed: C39.1, U10.7 (CPH)
unnamed: C39.2, U10.6 (CPL)
unnamed: R71.2, U10.21 (DRVOFF)
unnamed: R27.2, U10.40 (SOA)
unnamed: R28.2, U10.39 (SOB)
unnamed: R29.2, U10.38 (SOC)
VDD: J2.6, R56.1, R59.1; also elsewhere on the board

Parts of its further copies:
C9, C13, C15, C34, C38, C40, C88, C89: 100n; Nice_0402C
C10, C11, C12, C35, C36, C37: 100p; Nice_0402C
C16, C41: 1u; Nice_0603C
C17, C42: 100n; Nice_0603C
C19, C20, C44, C45, C72, C73, C75, C76: 10u; C_1206_3216Metric
C48, C87: 47n; Nice_0603C
C96, C97: 2.2u; Nice_0603C
J1, J3: Conn_02x06_Odd_Even; PinSocket_2x06_P2.54mm_Horizontal
R4, R5, R6, R7, R33, R34, R35, R36: 10k; Nice_0402R
R14, R15, R16, R43, R44, R45: 820R; Nice_0402R
R52, R65: 470R; Nice_0402R
R57, R58, R60, R61: 1k; Nice_0402R
R72, R73: 0R; Nice_0402R
TP11, TP12, TP14, TP15, TP17, TP18, TP20, TP21, TP23, TP24, TP26, TP27, TP29, TP30, TP32, TP33, TP35, TP36, TP38, TP39, TP41, TP42, TP44, TP45, TP47, TP48, TP50, TP51, TP61, TP62, TP64, TP65, TP67, TP68, TP70, TP71, TP73, TP74, TP76, TP77: TestPoint; TP_0.6mm
U2, U7: LM324; TSSOP-14_4.4x5mm_P0.65mm
U15, U16: DRV8316CR; VQFN40_RGF_TEX; MPN DRV8316CRRGFR

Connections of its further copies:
/MCU/TIM3_CH1: TP12.1, U16.27 (INHA); also elsewhere on the board
/MCU/TIM3_CH2: TP15.1, U16.28 (INLA); also elsewhere on the board
/MCU/TIM3_CH3: TP23.1, U15.31 (INHC); also elsewhere on the board
/MCU/TIM3_CH4: TP26.1, U15.32 (INLC); also elsewhere on the board
/MCU/TIM5_CH1: TP11.1, U15.27 (INHA); also elsewhere on the board
/MCU/TIM5_CH2: TP14.1, U15.28 (INLA); also elsewhere on the board
/MCU/TIM5_CH3: TP17.1, U15.29 (INHB); also elsewhere on the board
/MCU/TIM5_CH4: TP20.1, U15.30 (INLB); also elsewhere on the board
/MCU/TIM8_CH1: TP27.1, U16.32 (INLC); also elsewhere on the board
/MCU/TIM8_CH2: TP24.1, U16.31 (INHC); also elsewhere on the board
/MCU/TIM8_CH3: TP21.1, U16.30 (INLB); also elsewhere on the board
/MCU/TIM8_CH4: TP18.1, U16.29 (INHB); also elsewhere on the board
/Motor1/VM: C16.1, C17.1, C19.1, C20.1, C41.1, C42.1, C44.1, C45.1, C72.1, C73.1, C75.1, C76.1, U15.9 (VM), U15.10 (VM), U15.11 (VM), U16.9 (VM), U16.10 (VM), U16.11 (VM); also elsewhere on the board
/Motor2/MTR_AVDD: C13.1, C96.1, U2.4 (V+), U15.25 (AVDD)
/Motor2/NTC: C88.1, J1.2, R5.1, U2.3 (+)
/Motor2/U: U15.13 (OUTA), U15.14 (OUTA); also elsewhere on the board
/Motor2/V: U15.16 (OUTB), U15.17 (OUTB); also elsewhere on the board
/Motor2/W: U15.19 (OUTC), U15.20 (OUTC); also elsewhere on the board
/Motor3/MTR_AVDD: C38.1, C97.1, U7.4 (V+), U16.25 (AVDD)
/Motor3/NTC: C89.1, J3.2, R34.1, U7.3 (+)
/Motor3/U: U16.13 (OUTA), U16.14 (OUTA); also elsewhere on the board
/Motor3/V: U16.16 (OUTB), U16.17 (OUTB); also elsewhere on the board
/Motor3/W: U16.19 (OUTC), U16.20 (OUTC); also elsewhere on the board
GND: C9.2, C10.2, C11.2, C12.2, C13.2, C15.2, C17.2, C19.2, C20.2, C34.2, C35.2, C36.2, C37.2, C38.2, C40.2, C42.2, C44.2, C45.2, C72.2, C73.2, C75.2, C76.2, C88.2, C89.2, C96.2, C97.2, J1.3, J1.5, J3.3, J3.5, R5.2, R7.2, R34.2, R36.2, R72.1, R73.1, U2.11 (V-), U7.11 (V-), U15.2 (AGND), U15.4 (GND_BK), U15.12 (PGND), U15.15 (PGND), U15.18 (PGND), U15.26 (AGND), U15.EPAD, U16.2 (AGND), U16.4 (GND_BK), U16.12 (PGND), U16.15 (PGND), U16.18 (PGND), U16.26 (AGND), U16.EPAD; also elsewhere on the board
MTR2_FAULT: TP29.1, U15.22 (nFAULT); also elsewhere on the board
MTR2_MISO: J1.9, R52.1, TP73.1, U15.33 (SDO); also elsewhere on the board
MTR2_MOSI: J1.11, R52.2, TP70.1, U15.34 (SDI); also elsewhere on the board
MTR2_NCS: J1.12, TP67.1; also elsewhere on the board
MTR2_SCK: J1.7, TP76.1, U15.35 (SCLK); also elsewhere on the board
MTR2_SCL: J1.8, R57.2, TP64.1; also elsewhere on the board
MTR2_SDA: J1.10, R60.2, TP61.1; also elsewhere on the board
MTR2_SOA: TP41.1, U2.13 (-), U2.14; also elsewhere on the board
MTR2_SOB: TP44.1, U2.8, U2.9 (-); also elsewhere on the board
MTR2_SOC: TP47.1, U2.6 (-), U2.7; also elsewhere on the board
MTR2_TEMP: R4.2, TP50.1, U2.1; also elsewhere on the board
MTR2_WIPER: C9.1, J1.1; also elsewhere on the board
MTR3_FAULT: TP30.1, U16.22 (nFAULT); also elsewhere on the board
MTR3_MISO: J3.9, R65.1, TP74.1, U16.33 (SDO); also elsewhere on the board
MTR3_MOSI: J3.11, R65.2, TP71.1, U16.34 (SDI); also elsewhere on the board
MTR3_NCS: J3.12, TP68.1; also elsewhere on the board
MTR3_SCK: J3.7, TP77.1, U16.35 (SCLK); also elsewhere on the board
MTR3_SCL: J3.8, R58.2, TP65.1; also elsewhere on the board
MTR3_SDA: J3.10, R61.2, TP62.1; also elsewhere on the board
MTR3_SOA: TP42.1, U7.13 (-), U7.14; also elsewhere on the board
MTR3_SOB: TP45.1, U7.8, U7.9 (-); also elsewhere on the board
MTR3_SOC: TP48.1, U7.6 (-), U7.7; also elsewhere on the board
MTR3_TEMP: R33.2, TP51.1, U7.1; also elsewhere on the board
MTR3_WIPER: C34.1, J3.1; also elsewhere on the board
MTR_VREF: C15.1, C40.1, J1.4, J3.4, R6.1, R35.1, U15.37 (VREF/ILIM), U16.37 (VREF/ILIM); also elsewhere on the board
MTRx_DRV_nCS: U15.36 (nSCS), U16.36 (nSCS); also elsewhere on the board
MTRx_SLEEP: U15.23 (nSLEEP), U16.23 (nSLEEP); also elsewhere on the board
unnamed: R4.1, R6.2, R7.1, U2.2 (-)
unnamed: C12.1, R16.1, TP38.1, U2.5 (+)
unnamed: C11.1, R15.1, TP35.1, U2.10 (+)
unnamed: C10.1, R14.1, TP32.1, U2.12 (+)
unnamed: R33.1, R35.2, R36.1, U7.2 (-)
unnamed: C37.1, R45.1, TP39.1, U7.5 (+)
unnamed: C36.1, R44.1, TP36.1, U7.10 (+)
unnamed: C35.1, R43.1, TP33.1, U7.12 (+)
unnamed: C16.2, U15.8 (CP)
unnamed: C48.1, U15.7 (CPH)
unnamed: C48.2, U15.6 (CPL)
unnamed: R72.2, U15.21 (DRVOFF)
unnamed: R14.2, U15.40 (SOA)
unnamed: R15.2, U15.39 (SOB)
unnamed: R16.2, U15.38 (SOC)
unnamed: C41.2, U16.8 (CP)
unnamed: C87.1, U16.7 (CPH)
unnamed: C87.2, U16.6 (CPL)
unnamed: R73.2, U16.21 (DRVOFF)
unnamed: R43.2, U16.40 (SOA)
unnamed: R44.2, U16.39 (SOB)
unnamed: R45.2, U16.38 (SOC)
VDD: J1.6, J3.6, R57.1, R58.1, R60.1, R61.1; also elsewhere on the board

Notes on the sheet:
50V
Angle Sensor: TLI5012B - 48us update time (spi) AS5600 - 150us update time (i2c)
6V3
16V
This component is only placed for Motor channel 1!

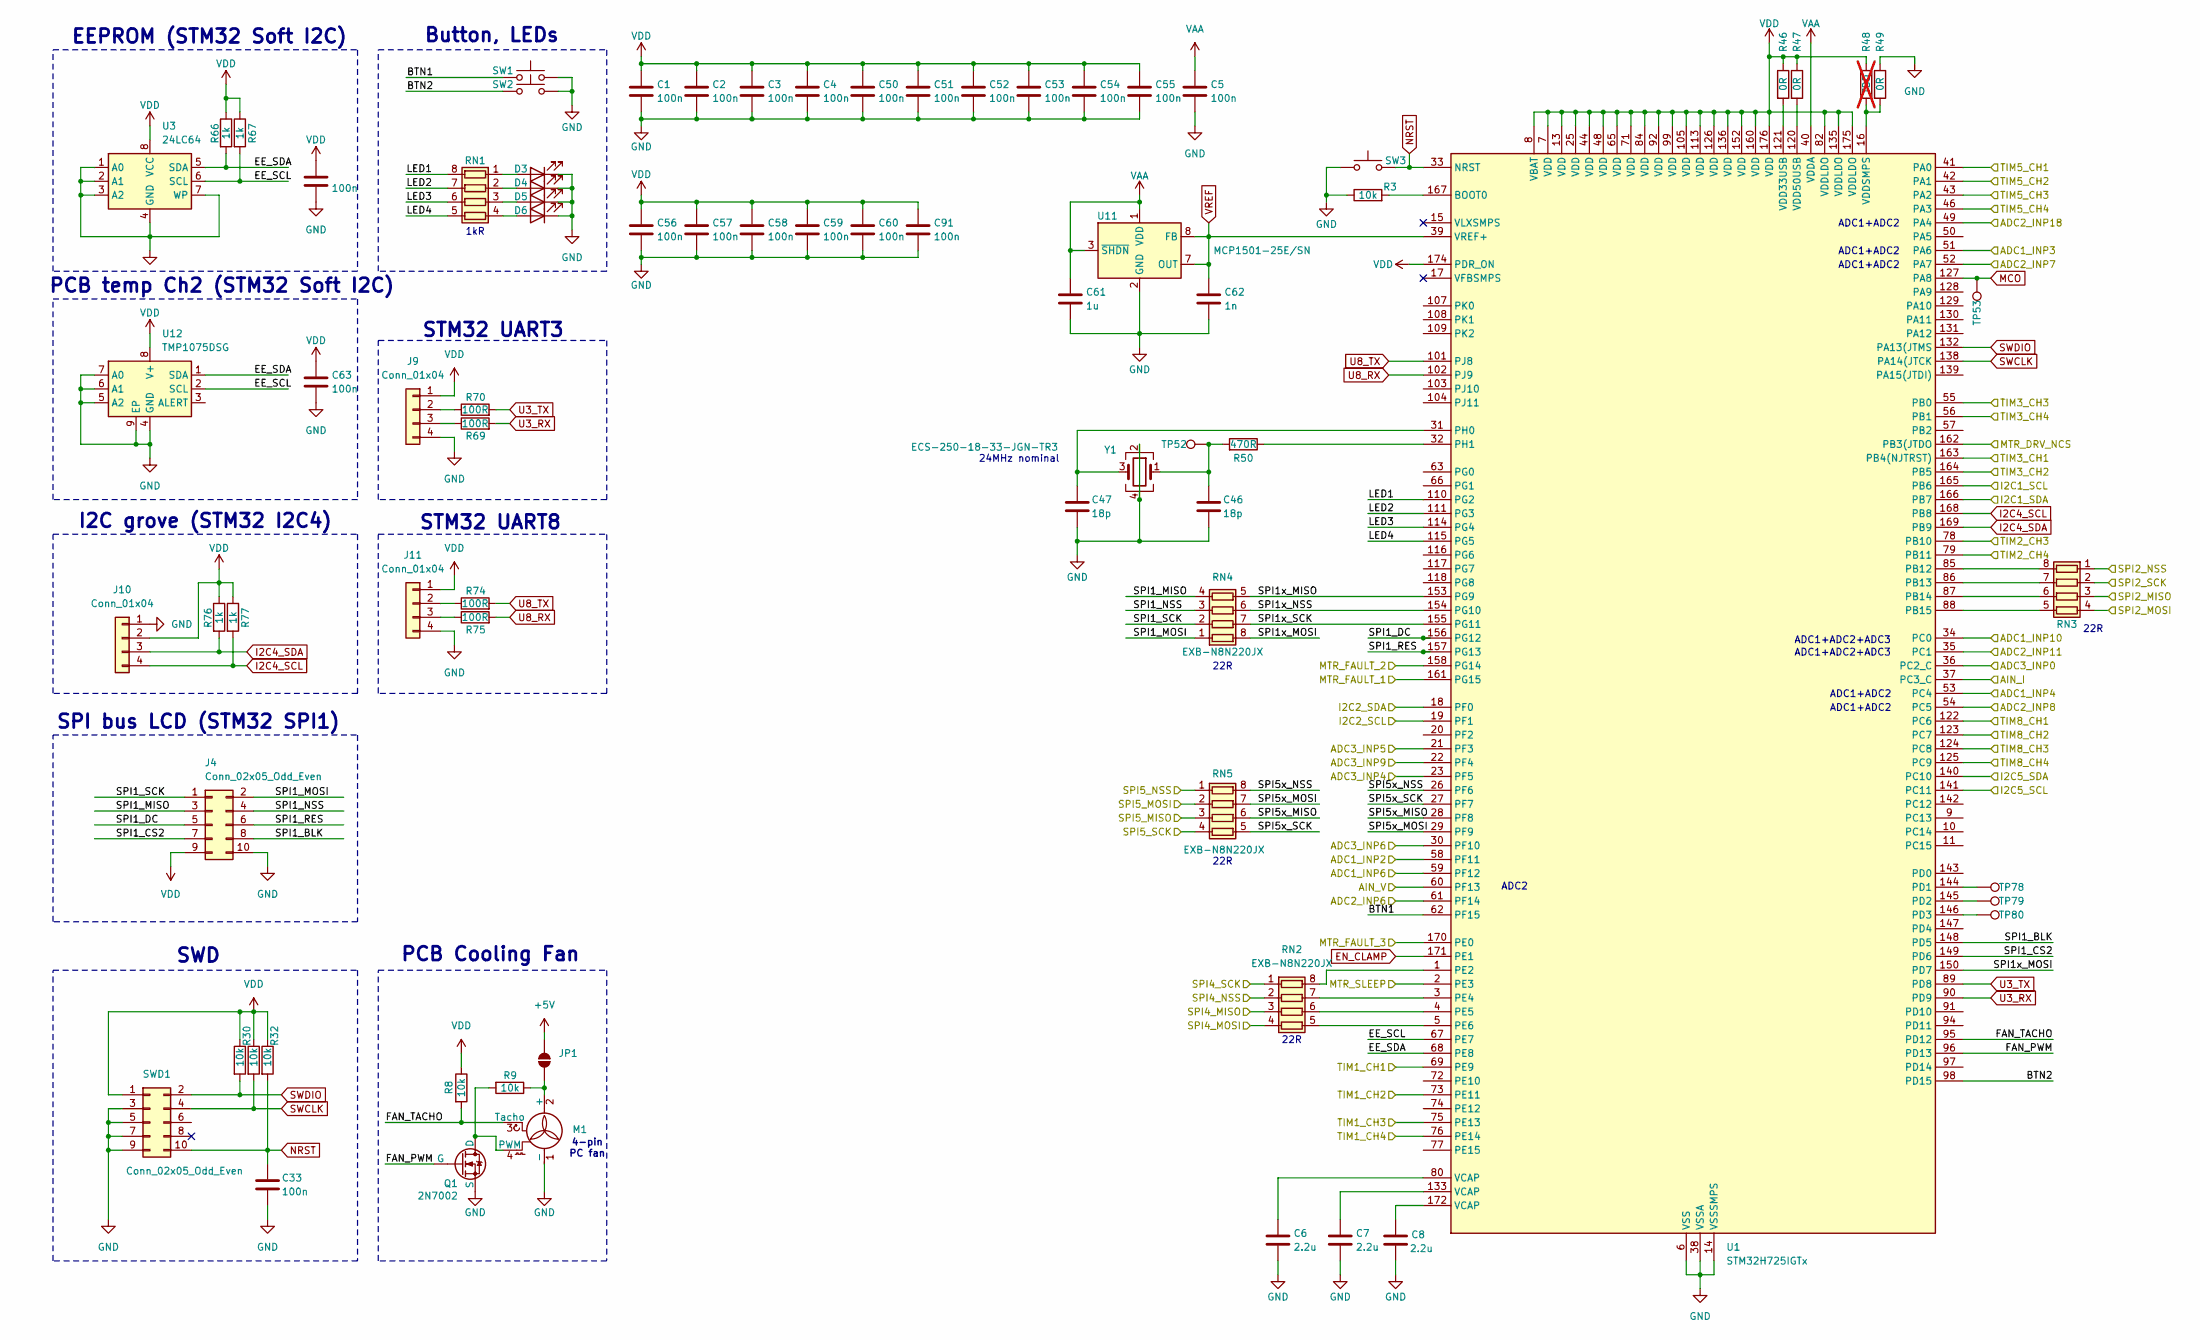
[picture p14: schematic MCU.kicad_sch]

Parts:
C1, C2, C3, C4, C5, C33, C49, C50, C51, C52, C53, C54, C55, C56, C57, C58, C59, C60, C63, C91: 100n; Nice_0402C
C6, C7, C8: 2.2u; Nice_0603C
C46, C47: 18p; Nice_0402C
C61: 1u; Nice_0603C
C62: 1n; Nice_0402C
D3, D4, D5, D6: APT2012SYCK; LED_0805_2012Metric; MPN APT2012SYCK
J4: Conn_02x05_Odd_Even; PinHeader_2x05_P2.54mm_Vertical
J9, J11: Conn_01x04; PinHeader_1x04_P2.54mm_Vertical
J10: Conn_01x04; JST_PH_B4B-PH-K_1x04_P2.00mm_Vertical
JP1: SolderJumper_2_Open; SolderJumper-2_P1.3mm_Open_Pad1.0x1.5mm
M1: Fan_Tacho_PWM; FanPinHeader_1x04_P2.54mm_Vertical
Q1: 2N7002; SOT-23
R3, R8, R9, R30, R31, R32: 10k; Nice_0402R
R46, R47, R49: 0R; Nice_0402R
R48: TBD; Nice_0402DNP; not fitted
R50: 470R; Nice_0402R
R66, R67, R76, R77: 1k; Nice_0402R
R69, R70, R74, R75: 100R; Nice_0402R
RN1: EXB-38V102JV; R_Array_Convex_4x0603
RN2, RN3, RN4, RN5: EXB-N8N220JX; R_Array_Concave_4x0402
SW1, SW2, SW3: SW_Push; SW_PUSH_1P1T_6x3.5mm_H5.0_APEM_MJTP1250
SWD1: Conn_02x05_Odd_Even; PinHeader_2x05_P1.27mm_Vertical_SMD
TP52, TP53, TP78, TP79, TP80: TestPoint; TP_0.6mm
U1: STM32H725IGTx; LQFP-176_24x24mm_P0.5mm
U3: 24LC64; SOIC-8_3.9x4.9mm_P1.27mm
U11: MCP1501-25E/SN; SOIC-8_3.9x4.9mm_P1.27mm; MPN MCP1501-25E/SN
U12: TMP1075DSG; WSON-8-1EP_2x2mm_P0.5mm_EP0.9x1.6mm_ThermalVias
Y1: ECS-250-18-33-JGN-TR3; Crystal_SMD_3225-4Pin_3.2x2.5mm; MPN ECS-250-18-33-JGN-TR3

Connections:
+5V: JP1.2 (B); also elsewhere on the board
/MCU/AIN_I: U1.37 (PC3_C); also elsewhere on the board
/MCU/AIN_V: U1.60 (PF13); also elsewhere on the board
/MCU/BTN1: SW1.2, U1.62 (PF15)
/MCU/BTN2: SW2.2, U1.98 (PD15)
/MCU/EE_SCL: R67.2, U1.67 (PE7), U3.6 (SCL), U12.2 (SCL)
/MCU/EE_SDA: R66.2, U1.68 (PE8), U3.5 (SDA), U12.1 (SDA)
/MCU/FAN_PWM: Q1.1 (G), U1.96 (PD13)
/MCU/FAN_TACHO: M1.3 (Tacho), R8.2, U1.95 (PD12)
/MCU/LED1: RN1.8 (R1.2), U1.110 (PG2)
/MCU/LED2: RN1.7 (R2.2), U1.111 (PG3)
/MCU/LED3: RN1.6 (R3.2), U1.114 (PG4)
/MCU/LED4: RN1.5 (R4.2), U1.115 (PG5)
/MCU/SPI1_BLK: J4.8, U1.148 (PD5)
/MCU/SPI1_CS2: J4.7, U1.149 (PD6)
/MCU/SPI1_DC: J4.5, U1.156 (PG12)
/MCU/SPI1_MISO: J4.3, RN4.4 (R4.1)
/MCU/SPI1_MOSI: J4.2, RN4.1 (R1.1)
/MCU/SPI1_NSS: J4.4, RN4.3 (R3.1)
/MCU/SPI1_RES: J4.6, U1.157 (PG13)
/MCU/SPI1_SCK: J4.1, RN4.2 (R2.1)
/MCU/SPI1x_MISO: RN4.5 (R4.2), U1.153 (PG9)
/MCU/SPI1x_MOSI: RN4.8 (R1.2), U1.150 (PD7)
/MCU/SPI1x_NSS: RN4.6 (R3.2), U1.154 (PG10)
/MCU/SPI1x_SCK: RN4.7 (R2.2), U1.155 (PG11)
/MCU/SPI5x_MISO: RN5.6 (R3.2), U1.28 (PF8)
/MCU/SPI5x_MOSI: RN5.7 (R2.2), U1.29 (PF9)
/MCU/SPI5x_NSS: RN5.8 (R1.2), U1.26 (PF6)
/MCU/SPI5x_SCK: RN5.5 (R4.2), U1.27 (PF7)
/MCU/TIM1_CH1: U1.69 (PE9); also elsewhere on the board
/MCU/TIM1_CH2: U1.73 (PE11); also elsewhere on the board
/MCU/TIM1_CH3: U1.75 (PE13); also elsewhere on the board
/MCU/TIM1_CH4: U1.76 (PE14); also elsewhere on the board
/MCU/TIM2_CH3: U1.78 (PB10); also elsewhere on the board
/MCU/TIM2_CH4: U1.79 (PB11); also elsewhere on the board
/MCU/TIM3_CH1: U1.163 (PB4(NJTRST)); also elsewhere on the board
/MCU/TIM3_CH2: U1.164 (PB5); also elsewhere on the board
/MCU/TIM3_CH3: U1.55 (PB0); also elsewhere on the board
/MCU/TIM3_CH4: U1.56 (PB1); also elsewhere on the board
/MCU/TIM5_CH1: U1.41 (PA0); also elsewhere on the board
/MCU/TIM5_CH2: U1.42 (PA1); also elsewhere on the board
/MCU/TIM5_CH3: U1.43 (PA2); also elsewhere on the board
/MCU/TIM5_CH4: U1.46 (PA3); also elsewhere on the board
/MCU/TIM8_CH1: U1.122 (PC6); also elsewhere on the board
/MCU/TIM8_CH2: U1.123 (PC7); also elsewhere on the board
/MCU/TIM8_CH3: U1.124 (PC8); also elsewhere on the board
/MCU/TIM8_CH4: U1.125 (PC9); also elsewhere on the board
EN_CLAMP: U1.171 (PE1); also elsewhere on the board
GND: C1.2, C2.2, C3.2, C4.2, C5.2, C6.2, C7.2, C8.2, C33.2, C46.2, C47.2, C49.2, C50.2, C51.2, C52.2, C53.2, C54.2, C55.2, C56.2, C57.2, C58.2, C59.2, C60.2, C61.2, C62.2, C63.2, C91.2, D3.1 (K), D4.1 (K), D5.1 (K), D6.1 (K), J4.10, J9.4, J10.1, J11.4, M1.1 (-), Q1.2 (S), R3.1, R49.1, SW1.1, SW2.1, SW3.1, SWD1.3, SWD1.5, SWD1.7, SWD1.9, U1.6 (VSS), U1.12 (VSS), U1.14 (VSSSMPS), U1.24 (VSS), U1.38 (VSSA), U1.45 (VSS), U1.47 (VSS), U1.64 (VSS), U1.70 (VSS), U1.81 (VSS), U1.83 (VSS), U1.93 (VSS), U1.100 (VSS), U1.106 (VSS), U1.112 (VSS), U1.119 (VSS), U1.134 (VSS), U1.137 (VSS), U1.151 (VSS), U1.159 (VSS), U1.173 (VSS), U3.1 (A0), U3.2 (A1), U3.3 (A2), U3.4 (GND), U3.7 (WP), U11.2 (GND), U11.4 (GND), U11.5 (GND), U11.6 (GND), U12.4 (GND), U12.5 (A2), U12.6 (A1), U12.7 (A0), U12.9 (EP), Y1.2, Y1.4; also elsewhere on the board
I2C4_SCL: J10.4, R77.2, U1.168 (PB8)
I2C4_SDA: J10.3, R76.2, U1.169 (PB9)
MCO: TP53.1, U1.127 (PA8)
MTR1_FAULT: U1.161 (PG15); also elsewhere on the board
MTR1_MISO: RN3.3 (R3.1); also elsewhere on the board
MTR1_MOSI: RN3.4 (R4.1); also elsewhere on the board
MTR1_NCS: RN3.1 (R1.1); also elsewhere on the board
MTR1_SCK: RN3.2 (R2.1); also elsewhere on the board
MTR1_SCL: U1.165 (PB6); also elsewhere on the board
MTR1_SDA: U1.166 (PB7); also elsewhere on the board
MTR1_SOA: U1.58 (PF11); also elsewhere on the board
MTR1_SOB: U1.51 (PA6); also elsewhere on the board
MTR1_SOC: U1.53 (PC4); also elsewhere on the board
MTR1_TEMP: U1.34 (PC0); also elsewhere on the board
MTR1_WIPER: U1.59 (PF12); also elsewhere on the board
MTR2_FAULT: U1.158 (PG14); also elsewhere on the board
MTR2_MISO: RN2.3 (R3.1); also elsewhere on the board
MTR2_MOSI: RN2.4 (R4.1); also elsewhere on the board
MTR2_NCS: RN2.2 (R2.1); also elsewhere on the board
MTR2_SCK: RN2.1 (R1.1); also elsewhere on the board
MTR2_SCL: U1.19 (PF1); also elsewhere on the board
MTR2_SDA: U1.18 (PF0); also elsewhere on the board
MTR2_SOA: U1.61 (PF14); also elsewhere on the board
MTR2_SOB: U1.52 (PA7); also elsewhere on the board
MTR2_SOC: U1.54 (PC5); also elsewhere on the board
MTR2_TEMP: U1.35 (PC1); also elsewhere on the board
MTR2_WIPER: U1.49 (PA4); also elsewhere on the board
MTR3_FAULT: U1.170 (PE0); also elsewhere on the board
MTR3_MISO: RN5.3 (R3.1); also elsewhere on the board
MTR3_MOSI: RN5.2 (R2.1); also elsewhere on the board
MTR3_NCS: RN5.1 (R1.1); also elsewhere on the board
MTR3_SCK: RN5.4 (R4.1); also elsewhere on the board
MTR3_SCL: U1.141 (PC11); also elsewhere on the board
MTR3_SDA: U1.140 (PC10); also elsewhere on the board
MTR3_SOA: U1.23 (PF5); also elsewhere on the board
MTR3_SOB: U1.21 (PF3); also elsewhere on the board
MTR3_SOC: U1.30 (PF10); also elsewhere on the board
MTR3_TEMP: U1.36 (PC2_C); also elsewhere on the board
MTR3_WIPER: U1.22 (PF4); also elsewhere on the board
MTRx_DRV_nCS: U1.162 (PB3(JTDO); also elsewhere on the board
MTRx_SLEEP: U1.2 (PE3); also elsewhere on the board
NRST: C33.1, R32.2, SW3.2, SWD1.10, U1.33 (NRST)
unnamed: C6.1, U1.80 (VCAP)
unnamed: C7.1, U1.133 (VCAP)
unnamed: C8.1, U1.172 (VCAP)
unnamed: C46.1, R50.2, TP52.1, Y1.1
unnamed: D3.2 (A), RN1.1 (R1.1)
unnamed: D4.2 (A), RN1.2 (R2.1)
unnamed: D5.2 (A), RN1.3 (R3.1)
unnamed: D6.2 (A), RN1.4 (R4.1)
unnamed: J9.2, R70.1
unnamed: J9.3, R69.1
unnamed: J11.2, R74.1
unnamed: J11.3, R75.1
unnamed: JP1.1 (A), M1.2 (+), R9.1
unnamed: M1.4 (PWM), Q1.3 (D), R9.2
unnamed: RN2.8 (R1.2), U1.1 (PE2)
unnamed: RN2.7 (R2.2), U1.3 (PE4)
unnamed: RN2.6 (R3.2), U1.4 (PE5)
unnamed: RN2.5 (R4.2), U1.5 (PE6)
unnamed: RN3.8 (R1.2), U1.85 (PB12)
unnamed: RN3.7 (R2.2), U1.86 (PB13)
unnamed: RN3.6 (R3.2), U1.87 (PB14)
unnamed: RN3.5 (R4.2), U1.88 (PB15)
unnamed: R3.2, U1.167 (BOOT0)
unnamed: TP78.1, U1.144 (PD1)
unnamed: TP79.1, U1.145 (PD2)
unnamed: TP80.1, U1.146 (PD3)
unnamed: C47.1, U1.31 (PH0), Y1.3
unnamed: R50.1, U1.32 (PH1)
unnamed: R46.2, U1.121 (VDD33USB)
unnamed: R47.2, U1.120 (VDD50USB)
unnamed: R48.2, R49.2, U1.16 (VDDSMPS)
SWCLK: R31.2, SWD1.4, U1.138 (PA14(JTCK)
SWDIO: R30.2, SWD1.2, U1.132 (PA13(JTMS)
U3_RX: R69.2, U1.90 (PD9)
U3_TX: R70.2, U1.89 (PD8)
U8_RX: R75.2, U1.102 (PJ9)
U8_TX: R74.2, U1.101 (PJ8)
VAA: C5.1, C61.1, U1.40 (VDDA), U11.1 (VDD), U11.3 (~SHDN); also elsewhere on the board
VDD: C1.1, C2.1, C3.1, C4.1, C49.1, C50.1, C51.1, C52.1, C53.1, C54.1, C55.1, C56.1, C57.1, C58.1, C59.1, C60.1, C63.1, C91.1, J4.9, J9.1, J10.2, J11.1, R8.1, R30.1, R31.1, R32.1, R46.1, R47.1, R48.1, R66.1, R67.1, R76.1, R77.1, SWD1.1, U1.7 (VDD), U1.8 (VBAT), U1.13 (VDD), U1.25 (VDD), U1.44 (VDD), U1.48 (VDD), U1.65 (VDD), U1.71 (VDD), U1.82 (VDDLDO), U1.84 (VDD), U1.92 (VDD), U1.99 (VDD), U1.105 (VDD), U1.113 (VDD), U1.126 (VDD), U1.135 (VDDLDO), U1.136 (VDD), U1.152 (VDD), U1.160 (VDD), U1.174 (PDR_ON), U1.175 (VDDLDO), U1.176 (VDD), U3.8 (VCC), U12.8 (V+); also elsewhere on the board
VREF: C62.1, U1.39 (VREF+), U11.7 (OUT), U11.8 (FB)

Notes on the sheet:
ADC1+ADC2
24MHz nominal
ADC2
EEPROM (STM32 Soft I2C)
22R
STM32 UART3
1kR
I2C grove (STM32 I2C4)
Button, LEDs
PCB Cooling Fan
STM32 UART8
SWD
ADC1+ADC2+ADC3
SPI bus LCD (STM32 SPI1)
PCB temp Ch2 (STM32 Soft I2C)
4-pin PC fan

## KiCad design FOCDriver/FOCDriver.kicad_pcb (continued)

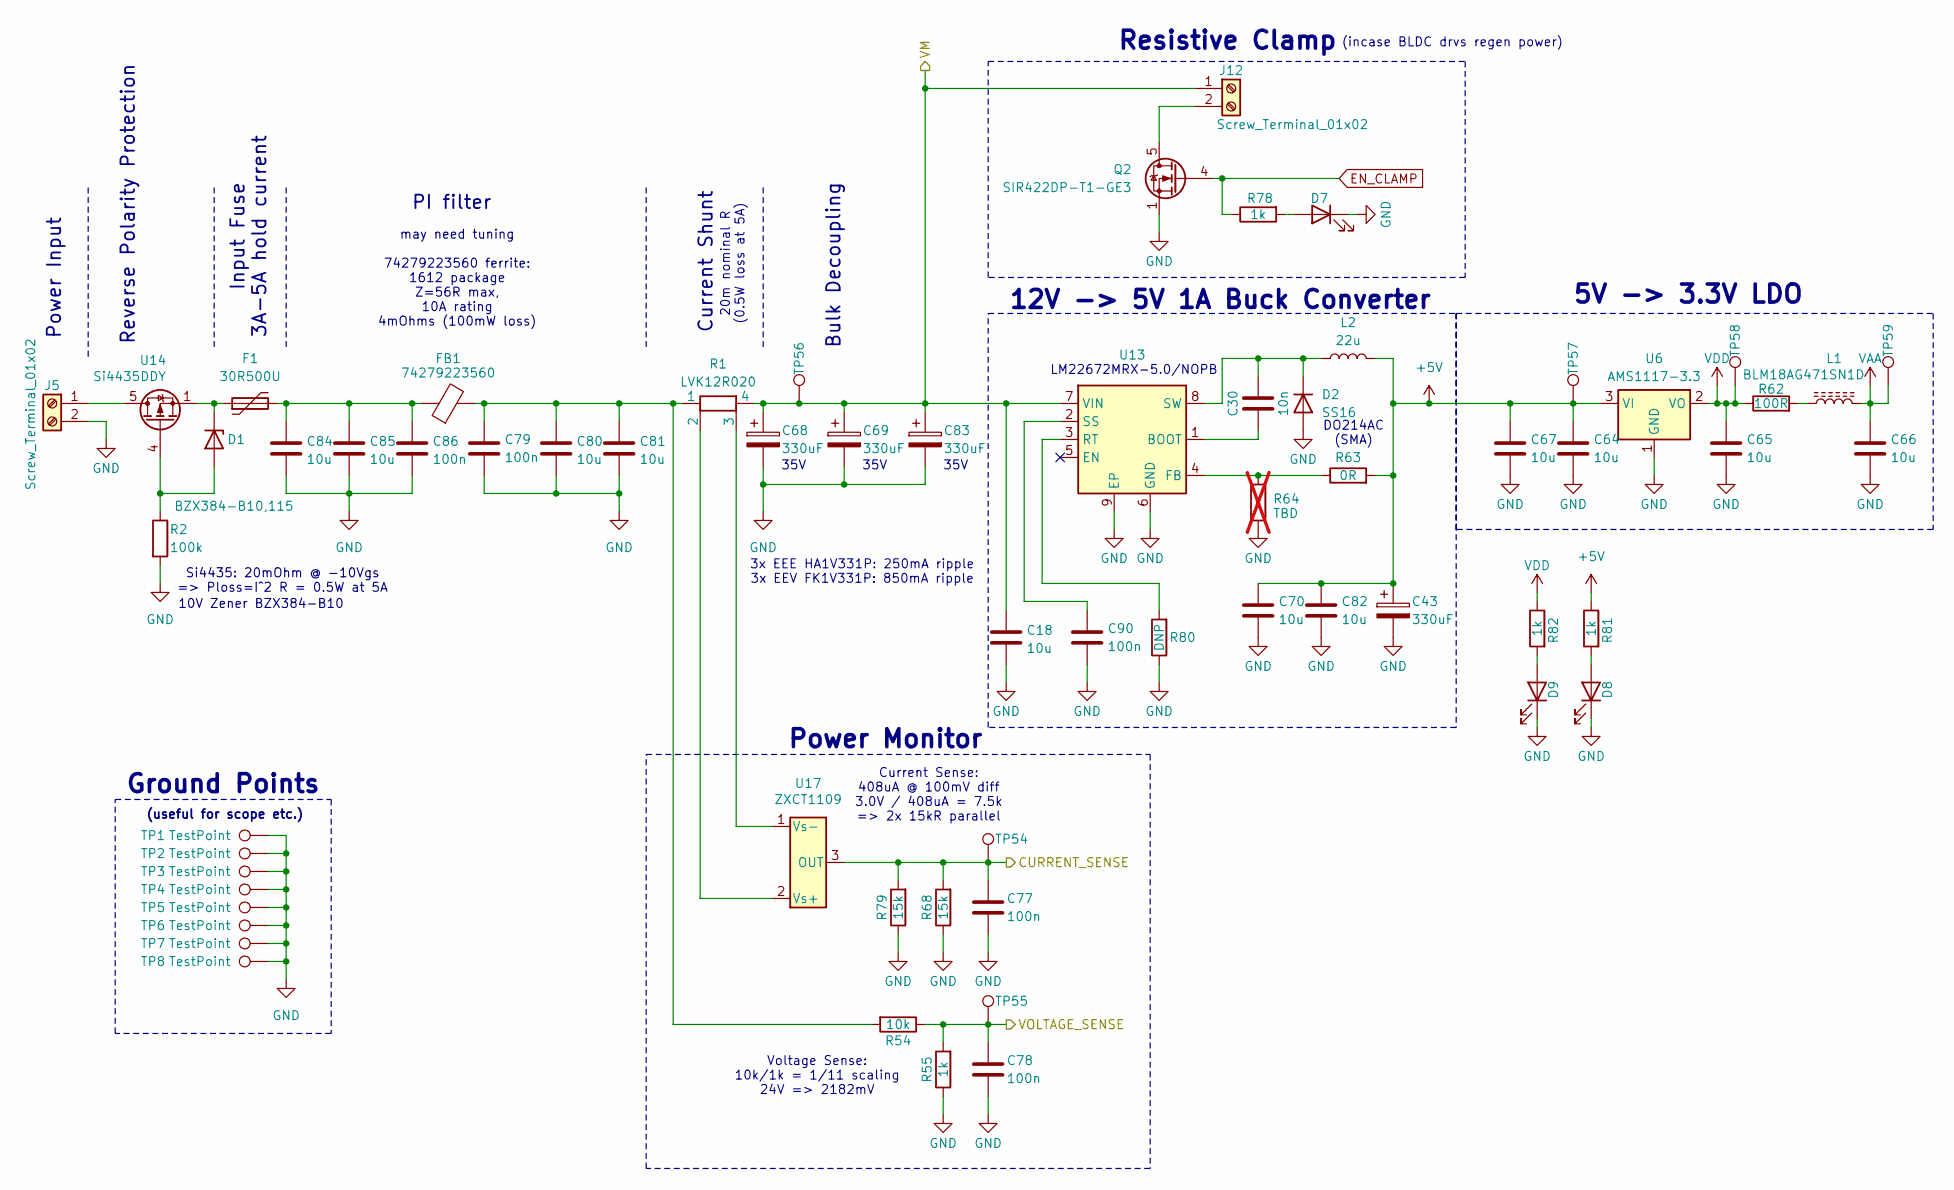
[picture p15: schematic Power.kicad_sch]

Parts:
C18, C64, C65, C66, C67, C70, C80, C81, C82, C84, C85: 10u; C_1206_3216Metric
C30: 10n; Nice_0603C
C43: 330uF; CP_Elec_8x10.5; MPN EEEFT1V331AP
C68, C69, C83: 330uF; CP_Elec_10x10.5; MPN EEV FK1V331P
C77, C78: 100n; Nice_0402C
C79, C86, C90: 100n; Nice_0603C
D1: BZX384-B10,115; D_SOD-323_HandSoldering; MPN BZX384-B10,115
D2: SS16; D_SMA
D7, D8, D9: APT2012SYCK; LED_0805_2012Metric; MPN APT2012SYCK
F1: 30R500U; LIttelfuse_30R
FB1: 74279223560; L_1812_4532Metric
J5, J12: Screw_Terminal_01x02; TerminalBlock_Phoenix_MKDS-1,5-2_1x02_P5.00mm_Horizontal
L1: BLM18AG471SN1D; L_0805_2012Metric
L2: 22u; L_Bourns-SRN8040_8x8.15mm; MPN SRN8040-220M
Q2: SIR422DP-T1-GE3; PowerPAK_SO-8_Single
R1: LVK12R020; R_Shunt_Ohmite_LVK12; MPN LVK12R020CER
R2: 100k; Nice_0402R
R54: 10k; Nice_0402R
R55, R78, R81, R82: 1k; Nice_0402R
R62: 100R; Nice_0402R
R63: 0R; Nice_0402R
R64: TBD; Nice_0402DNP; not fitted
R68, R79: 15k; Nice_0402R
R80: DNP; Nice_0402DNP
TP1, TP2, TP3, TP4, TP5, TP6, TP7, TP8: TestPoint; TestPoint_THTPad_D1.0mm_Drill0.5mm
TP54, TP55, TP56, TP57, TP58, TP59: TestPoint; TP_0.6mm
U6: AMS1117-3.3; SOT-223-3_TabPin2
U13: LM22676MR-5; TI_SO-PowerPAD-8; MPN LM22672MRX-5.0/NOPB
U14: Si4435DDY; SOIC-8_3.9x4.9mm_P1.27mm
U17: ZXCT1109; SOT-23; MPN ZXCT1109SA-7

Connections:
+5V: C43.1, C64.1, C67.1, C70.1, C82.1, L2.2, R63.2, R81.1, TP57.1, U6.3 (VI); also elsewhere on the board
/MCU/AIN_I: C77.1, R68.2, R79.2, TP54.1, U17.3 (OUT); also elsewhere on the board
/MCU/AIN_V: C78.1, R54.1, R55.2, TP55.1; also elsewhere on the board
/Motor1/VM: C18.1, C68.1, C69.1, C83.1, J12.1, R1.4, TP56.1, U13.7 (VIN); also elsewhere on the board
EN_CLAMP: Q2.4 (G), R78.1; also elsewhere on the board
GND: C18.2, C43.2, C64.2, C65.2, C66.2, C67.2, C68.2, C69.2, C70.2, C77.2, C78.2, C79.2, C80.2, C81.2, C82.2, C83.2, C84.2, C85.2, C86.2, C90.2, D2.2 (A), D7.1 (K), D8.1 (K), D9.1 (K), J5.2, Q2.1 (S), Q2.2 (S), Q2.3 (S), R2.2, R55.1, R64.2, R68.1, R79.1, R80.1, TP1.1, TP2.1, TP3.1, TP4.1, TP5.1, TP6.1, TP7.1, TP8.1, U6.1 (GND), U13.6 (GND), U13.9 (EP); also elsewhere on the board
unnamed: C79.1, C80.1, C81.1, FB1.2, R1.1, R54.2
unnamed: C84.1, C85.1, C86.1, F1.2, FB1.1
unnamed: D1.2 (A), R2.1, U14.4 (G)
unnamed: D1.1 (K), F1.1, U14.1 (S), U14.2 (S), U14.3 (S)
unnamed: C30.2, D2.1 (K), L2.1, U13.8 (SW)
unnamed: D7.2 (A), R78.2
unnamed: D8.2 (A), R81.2
unnamed: D9.2 (A), R82.2
unnamed: J5.1, U14.5 (D), U14.6 (D), U14.7 (D), U14.8 (D)
unnamed: J12.2, Q2.5 (D)
unnamed: L1.1, R62.2
unnamed: C30.1, U13.1 (BOOT)
unnamed: R63.1, R64.1, U13.4 (FB)
unnamed: R80.2, U13.3 (RT)
unnamed: C90.1, U13.2 (SS)
unnamed: R1.2, U17.2 (Vs+)
unnamed: R1.3, U17.1 (Vs-)
VAA: C66.1, L1.2, TP59.1; also elsewhere on the board
VDD: C65.1, R62.1, R82.1, TP58.1, U6.2 (VO); also elsewhere on the board

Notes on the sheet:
(useful for scope etc.)
Current Shunt
DO214AC (SMA)
may need tuning 74279223560 ferrite: 1612 package Z=56R max, 10A rating 4mOhms (100mW loss)
35V
3x EEE HA1V331P: 250mA ripple 3x EEV FK1V331P: 850mA ripple
(incase BLDC drvs regen power)
Power Input
Input Fuse 3A-5A hold current
Resistive Clamp
Power Monitor
LM22672MRX-5.0/NOPB
Bulk Decoupling
Ground Points
10V Zener BZX384-B10
12V -> 5V 1A Buck Converter
Voltage Sense: 10k/1k = 1/11 scaling 24V => 2182mV
Si4435: 20mOhm @ -10Vgs => Ploss=I^2 R = 0.5W at 5A
5V -> 3.3V LDO
PI filter
20m nominal R (0.5W loss at 5A)
Reverse Polarity Protection
Current Sense: 408uA @ 100mV diff 3.0V / 408uA = 7.5k => 2x 15kR parallel

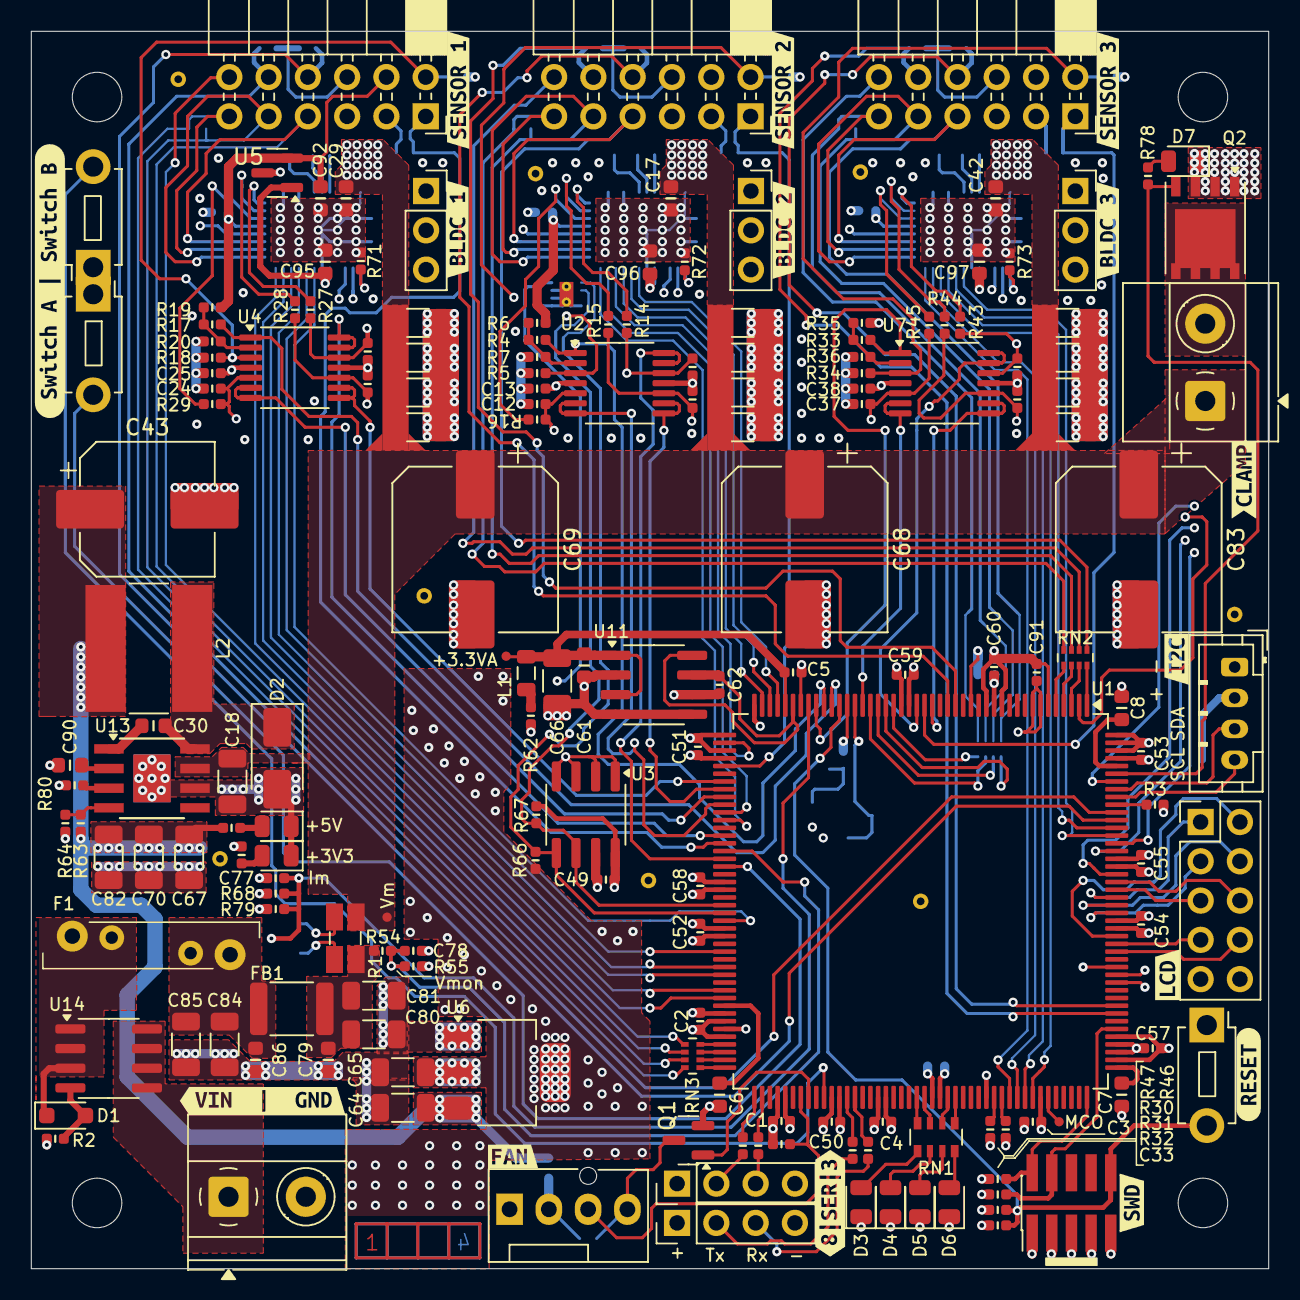
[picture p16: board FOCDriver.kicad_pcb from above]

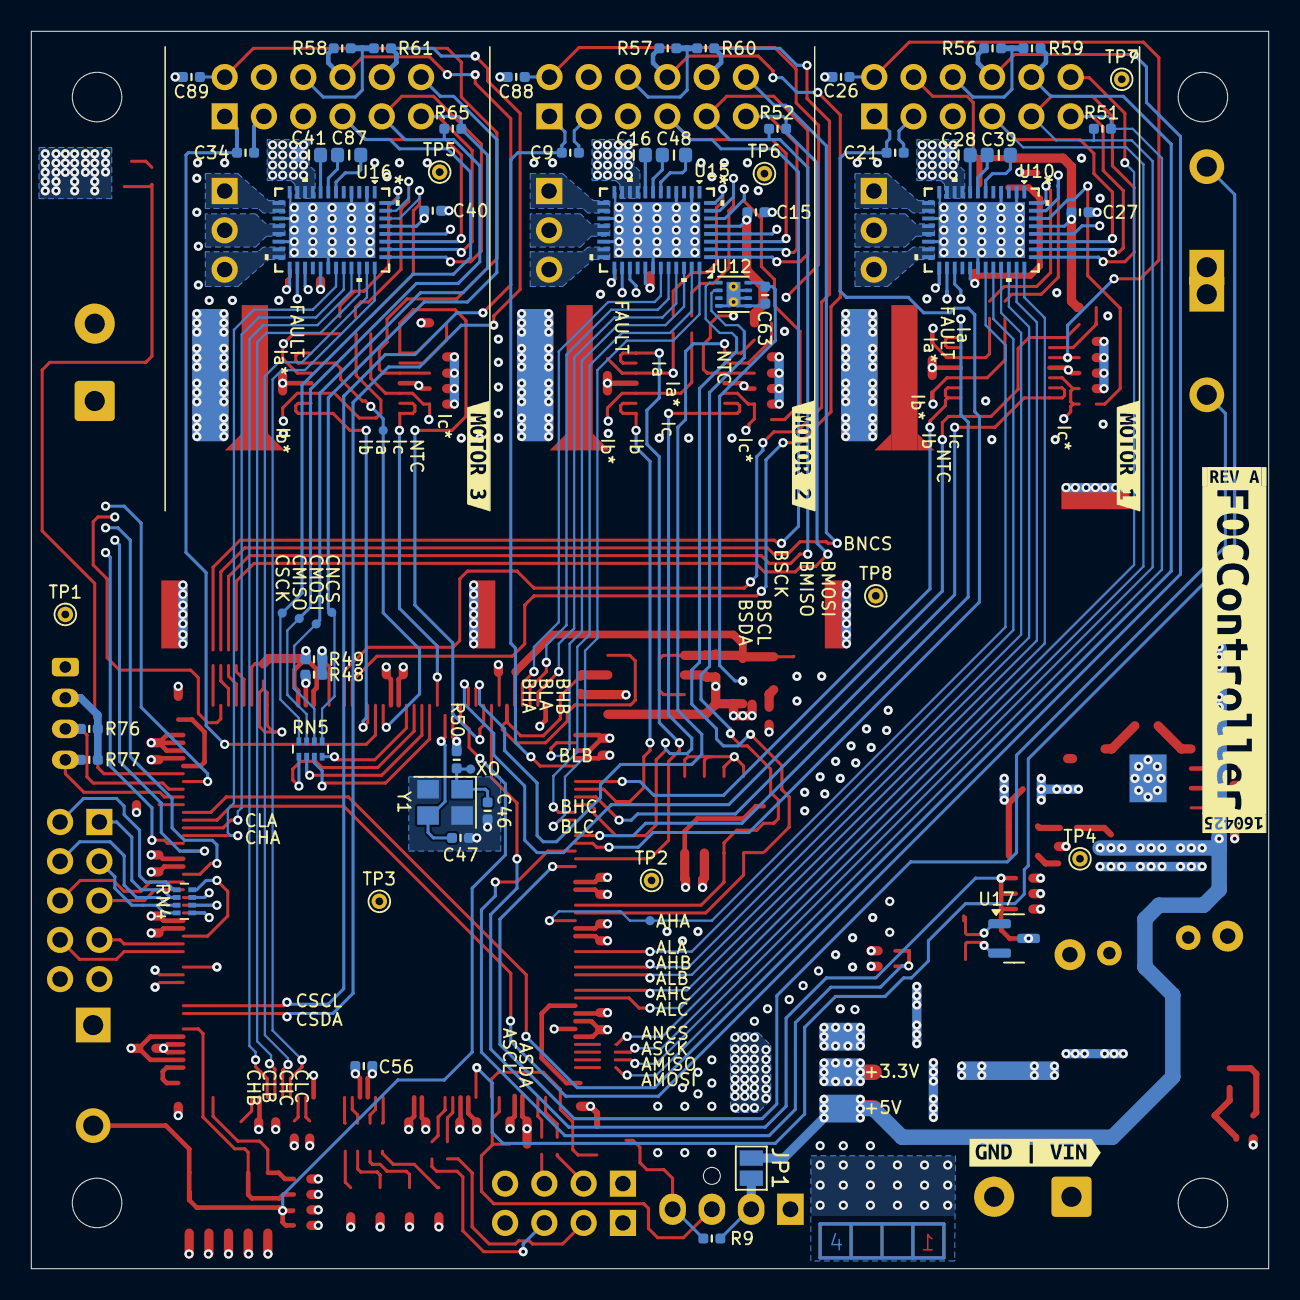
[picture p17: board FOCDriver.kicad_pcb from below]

Board: 4 copper layers, 80.0 x 80.0 mm, 318 parts (124 on the bottom side), 198 nets.

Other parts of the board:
kibuzzard-67EC00B3: G***; kibuzzard-67EC00B3
kibuzzard-67ED282B: G***; kibuzzard-67ED282B
kibuzzard-67F3CA67: G***; kibuzzard-67F3CA67
kibuzzard-67F3CAB6: G***; kibuzzard-67F3CAB6
kibuzzard-67F3CB42: G***; kibuzzard-67F3CB42
kibuzzard-67F3CD14: G***; kibuzzard-67F3CD14
kibuzzard-67F3CD28: G***; kibuzzard-67F3CD28
kibuzzard-67F3CD42: G***; kibuzzard-67F3CD42
kibuzzard-67F3CD48: G***; kibuzzard-67F3CD48
kibuzzard-67F3CD55: G***; kibuzzard-67F3CD55
kibuzzard-67F3CD63: G***; kibuzzard-67F3CD63
kibuzzard-67F3FE9D: G***; kibuzzard-67F3FE9D
kibuzzard-67F3FEBC: G***; kibuzzard-67F3FEBC
kibuzzard-67F3FEF2: G***; kibuzzard-67F3FEF2
kibuzzard-67F3FF37: G***; kibuzzard-67F3FF37
kibuzzard-67F6A3C3: G***; kibuzzard-67F6A3C3
kibuzzard-67F56438: G***; kibuzzard-67F56438
kibuzzard-67FA2A95: G***; kibuzzard-67FA2A95
kibuzzard-67FA3F2F: G***; kibuzzard-67FA3F2F
kibuzzard-67FE68DD: G***; kibuzzard-67FE68DD
kibuzzard-67FE6936: G***; kibuzzard-67FE6936
kibuzzard-67FE6963: G***; kibuzzard-67FE6963

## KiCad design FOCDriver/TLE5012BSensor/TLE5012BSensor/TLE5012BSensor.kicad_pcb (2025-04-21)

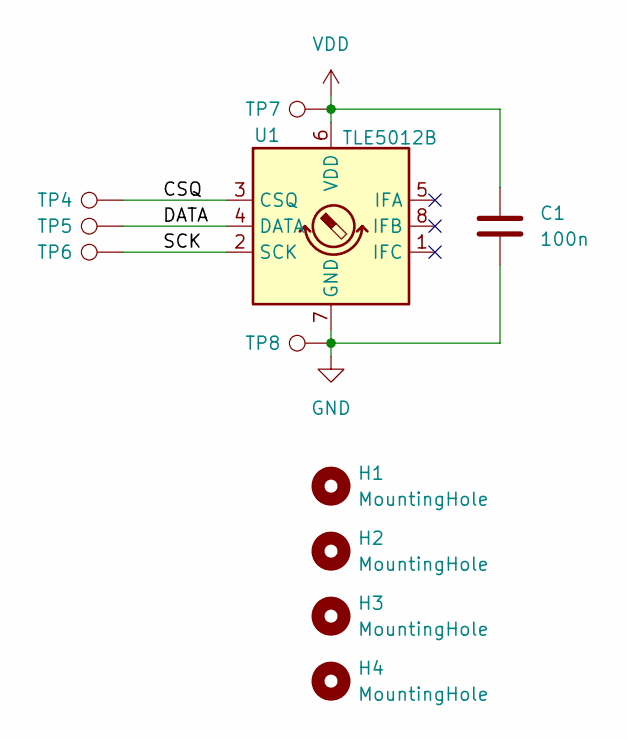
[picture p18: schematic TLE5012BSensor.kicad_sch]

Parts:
C1: 100n; Nice_0603C
H1, H2, H3, H4: MountingHole; MountingHole_3.2mm_M3
TP4, TP5, TP6, TP7, TP8: TestPoint; TestPoint_Pad_1.0x1.0mm
U1: TLE5012B; SOIC-8_3.9x4.9mm_P1.27mm

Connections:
/CSQ: TP4.1, U1.3 (CSQ)
/DATA: TP5.1, U1.4 (DATA)
/SCK: TP6.1, U1.2 (SCK)
GND: C1.2, TP8.1, U1.7 (GND)
VDD: C1.1, TP7.1, U1.6 (VDD)

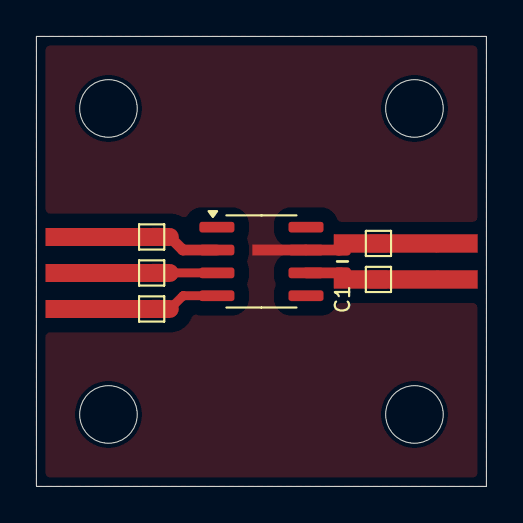
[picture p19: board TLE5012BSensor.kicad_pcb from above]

Board: 2 copper layers, 25.0 x 25.0 mm, 11 parts (0 on the bottom side), 5 nets.

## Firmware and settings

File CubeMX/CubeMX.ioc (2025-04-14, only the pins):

Mcu.UserName=STM32H725IGTx
PA0.Signal=S_TIM5_CH1
PA1.Signal=S_TIM5_CH2
PA13(JTMS/SWDIO).Signal=DEBUG_JTMS-SWDIO
PA14(JTCK/SWCLK).Signal=DEBUG_JTCK-SWCLK
PA2.Signal=S_TIM5_CH3
PA3.Signal=S_TIM5_CH4
PA4.Signal=ADCx_INP18
PA5.Signal=S_TIM2_CH1_ETR
PA6.Signal=ADCx_INP3
PA7.Signal=ADCx_INP7
PA8.Signal=RCC_MCO_1
PB0.Signal=S_TIM3_CH3
PB1.Signal=S_TIM3_CH4
PB10.Signal=S_TIM2_CH3
PB11.Signal=S_TIM2_CH4
PB12.Signal=SPI2_NSS
PB13.Signal=SPI2_SCK
PB14.Signal=SPI2_MISO
PB15.Signal=SPI2_MOSI
PB3(JTDO/TRACESWO).Signal=GPIO_Output
PB4(NJTRST).Signal=S_TIM3_CH1
PB5.Signal=S_TIM3_CH2
PB6.Signal=I2C1_SCL
PB7.Signal=I2C1_SDA
PB8.Signal=I2C4_SCL
PB9.Signal=I2C4_SDA
PC0.Signal=ADCx_INP10
PC1.Signal=ADCx_INP11
PC10.Signal=I2C5_SDA
PC11.Signal=I2C5_SCL
PC2_C.Signal=ADC3_INP0
PC3_C.Signal=ADC3_INP1
PC4.Signal=ADCx_INP4
PC5.Signal=ADCx_INP8
PC6.Signal=S_TIM8_CH1
PC7.Signal=S_TIM8_CH2
PC8.Signal=S_TIM8_CH3
PC9.Signal=S_TIM8_CH4
PD12.Signal=GPIO_Input
PD13.Signal=S_TIM4_CH2
PD15.Signal=GPIO_Output
PD5.Signal=GPIO_Output
PD6.Signal=GPIO_Output
PD7.Signal=SPI1_MOSI
PD8.Signal=USART3_TX
PD9.Signal=USART3_RX
PE0.Signal=GPIO_Input
PE1.Signal=GPIO_Output
PE11.Signal=S_TIM1_CH2
PE13.Signal=S_TIM1_CH3
PE14.Signal=S_TIM1_CH4
PE2.Signal=SPI4_SCK
PE4.Signal=SPI4_NSS
PE5.Signal=SPI4_MISO
PE6.Signal=SPI4_MOSI
PE7.Signal=GPIO_Output
PE8.Signal=GPIO_Output
PE9.Signal=S_TIM1_CH1
PF0.Signal=I2C2_SDA
PF1.Signal=I2C2_SCL
PF10.Signal=ADC3_INP6
PF11.Signal=ADC1_INP2
PF12.Signal=ADC1_INP6
PF13.Signal=ADC2_INP2
PF14.Signal=ADC2_INP6
PF15.Signal=GPIO_Input
PF3.Signal=ADC3_INP5
PF4.Signal=ADC3_INP9
PF5.Signal=ADC3_INP4
PF6.Signal=SPI5_NSS
PF7.Signal=SPI5_SCK
PF8.Signal=SPI5_MISO
PF9.Signal=SPI5_MOSI
PG10.Signal=SPI1_NSS
PG11.Signal=SPI1_SCK
PG12.Signal=GPIO_Output
PG13.Signal=GPIO_Output
PG14.Signal=GPIO_Input
PG15.Signal=GPIO_Input
PG2.Signal=GPIO_Output
PG3.Signal=GPIO_Output
PG4.Signal=GPIO_Output
PG5.Signal=GPIO_Output
PG9.Signal=SPI1_MISO
PH0-OSC_IN.Signal=RCC_OSC_IN
PH1-OSC_OUT.Signal=RCC_OSC_OUT
PJ8.Signal=UART8_TX
PJ9.Signal=UART8_RX

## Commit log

2025-04-21 Sensor PCB fixes labels
    [FOCDriver.kicad_pcb, FOCDriver.kicad_sch, MotorDriver.kicad_sch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]
2025-04-21 Untented vias for DRVOFF signal Added unallocated IOs for DRVOFF potentially
    [FOCDriver.kicad_pcb, MCU.kicad_sch, MotorDriver.kicad_sch]
2025-04-21 Ordered at Aisler
    [FOCDriver.kicad_pcb]
2025-08-28 Bill of materials
    [FOCDriver.csv]
